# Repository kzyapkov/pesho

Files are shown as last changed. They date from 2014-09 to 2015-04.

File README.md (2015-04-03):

# pesho

Named after St. Peter, the gatekeeper of the physical premises of initlab.org

The rest of this page is in Bulgarian and should not be read by anyone.

## Жици

Схемата включва:
 * **RaspberryPi B+**  на което работи демона за управление, свързано
   през етернет кабел за кораба-майка;
 * **DC Dual Motor Driver 30V 4A** -- драйвер за мотора в бравата,
     [линк](http://www.microbot.it/en/product/73/DC-Dual-Motor-Driver-30V-4A-V2.html)
 * **DC-DC Step-down** за да дадем 5V на малинката и
 * няколко оптрона и други пасивни компоненти.

[Схемата](https://raw.githubusercontent.com/kzyapkov/pesho/master/hardware/pesho.pdf),
начертана с KiCAD.

Накратко, Пешо чете 3 датчика на вратата:
 * "шиповете са извадени", на бравата BLK
 * "шиповете са прибрани", на бравата BUK
 * "вратата е затворена", на бравата BD
Пешо отключва и заключва бравата, като задвижва мотора за 200ms
в желаната посока.

## Код

На Go. Идеята е бравата да може да се манипулира чрез бутоните
и през HTTP. За тестове и дебъгване, HUP сигнал към процеса на
демона също ще отключи или заключи бравата.

## Строене

За успешен билд ти трябва Go Workspace, ето [как](https://golang.org/doc/code.html). После трябва
да упоменеш, че крос-компилираш за arm6:

    # tell go we're cross-compiling for arm6 (rpi):
    export GOOS=linux
    export GOARCH=arm
    export GOARM=6

и накрая, от тази директория:

    pwd
        ...github.com/kzyapkov/pesho
    go build .
    ls -al ./pesho

така получения `pesho` е статично линкнатото bin-че което седи
в /root/pesho и се пуска със `systemctl start pesho`.

## Следва

* Да следим захранването.

## License

      Copyright (c) 2014, initLab <vloo@initlab.org>
      All rights reserved.

      Redistribution and use in source and binary forms, with or without
      modification, are permitted provided that the following conditions are met:

      1. Redistributions of source code must retain the above copyright notice, this
         list of conditions and the following disclaimer.
      2. Redistributions in binary form must reproduce the above copyright notice,
         this list of conditions and the following disclaimer in the documentation
         and/or other materials provided with the distribution.

      THIS SOFTWARE IS PROVIDED BY THE COPYRIGHT HOLDERS AND CONTRIBUTORS "AS IS" AND
      ANY EXPRESS OR IMPLIED WARRANTIES, INCLUDING, BUT NOT LIMITED TO, THE IMPLIED
      WARRANTIES OF MERCHANTABILITY AND FITNESS FOR A PARTICULAR PURPOSE ARE
      DISCLAIMED. IN NO EVENT SHALL THE COPYRIGHT OWNER OR CONTRIBUTORS BE LIABLE FOR
      ANY DIRECT, INDIRECT, INCIDENTAL, SPECIAL, EXEMPLARY, OR CONSEQUENTIAL DAMAGES
      (INCLUDING, BUT NOT LIMITED TO, PROCUREMENT OF SUBSTITUTE GOODS OR SERVICES;
      LOSS OF USE, DATA, OR PROFITS; OR BUSINESS INTERRUPTION) HOWEVER CAUSED AND
      ON ANY THEORY OF LIABILITY, WHETHER IN CONTRACT, STRICT LIABILITY, OR TORT
      (INCLUDING NEGLIGENCE OR OTHERWISE) ARISING IN ANY WAY OUT OF THE USE OF THIS
      SOFTWARE, EVEN IF ADVISED OF THE POSSIBILITY OF SUCH DAMAGE.

      The views and conclusions contained in the software and documentation are those
      of the authors and should not be interpreted as representing official policies,
      either expressed or implied, of the FreeBSD Project.

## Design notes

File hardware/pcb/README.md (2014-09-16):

# Pesho PCB

### Hardware description:

 * Raspberry Pi
 * 3 optoizolated relays
 * 3 optoizolated inputs
 * pesho's pcb

### Design

The design is done using latest version of KiCAD from the repository.
All modules, that weren't available are in pesho.pretty folder.

### License: [Beerware][1]

```
/*
 * ----------------------------------------------------------------------------
 * "THE BEER-WARE LICENSE" (Revision 42):
 * <phk@FreeBSD.ORG> wrote this file. As long as you retain this notice you
 * can do whatever you want with this stuff. If we meet some day, and you think
 * this stuff is worth it, you can buy me a beer in return Poul-Henning Kamp
 * ----------------------------------------------------------------------------
 */
```

[1]: http://en.wikipedia.org/wiki/Beerware

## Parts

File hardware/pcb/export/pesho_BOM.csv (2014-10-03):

Id | Designator | Package | Quantity | Designation | Supplier and ref
1 | C1 | capacitors:CP_10x13mm | 1 | CE 220uF 50V 105C Fujicon
2 | C2,C3,C4,C5,C6,C7,C9,C10,C11,C13,C15,C16 | smd_capacitors:c_1206 | 12 | 10nF
3 | C8 | smd_capacitors:c_1206 | 1 | 10uF
4 | C12 | smd_capacitors:c_1206 | 1 | 100nF
5 | C14 | smd_capacitors:c_1206 | 1 | 100pF
6 | D1 | led:LED-5MM | 1 | LOCK
7 | D2 | led:LED-5MM | 1 | EN
8 | D3 | led:LED-5MM | 1 | UNLOCK
9 | D4 | led:LED-5MM | 1 | BUK
10 | D5 | led:LED-5MM | 1 | BD
11 | D6 | led:LED-5MM | 1 | BLK
12 | D7,D8,D9 | discret:D3 | 3 | SB560 YJ / 60V / 5A / Schottky
13 | D10,D11 | discret:D6.5 | 2 | SB560 YJ / 60V / 5A / Schottky
14 | IC1,IC2,IC3,IC4,IC5,IC6 | dip_sockets:DIP-6__300_ELL | 6 | 4N25
15 | JP1,JP2,JP3 | pin_array:PIN_ARRAY_3X1 | 3 | JUMPER
16 | P1 | pesho:HD-515R-2P | 1 | Power
17 | P2 | pesho:HD-515R-6P | 1 | Bulkey
18 | P3 | connect:HE10_26D | 1 | Raspberry Pi CONN
19 | P4 | connect:SIL-3 | 1 | Serial
20 | R1,R2,R3 | smd_capacitors:c_1206 | 3 | 2.7K
21 | R4,R5,R6 | smd_capacitors:c_1206 | 3 | 820
22 | RV1,RV2,RV3,RV4,RV5,RV6,RV7,RV8,RV9 | pesho:3968W | 9 | 3296W(64W) 20K DIV
23 | U1,U2,U3 | pesho:JE-112D | 3 | JE-112D
24 | D12,D13 | pesho:DO-214AB | 2 | UF5GC SMD

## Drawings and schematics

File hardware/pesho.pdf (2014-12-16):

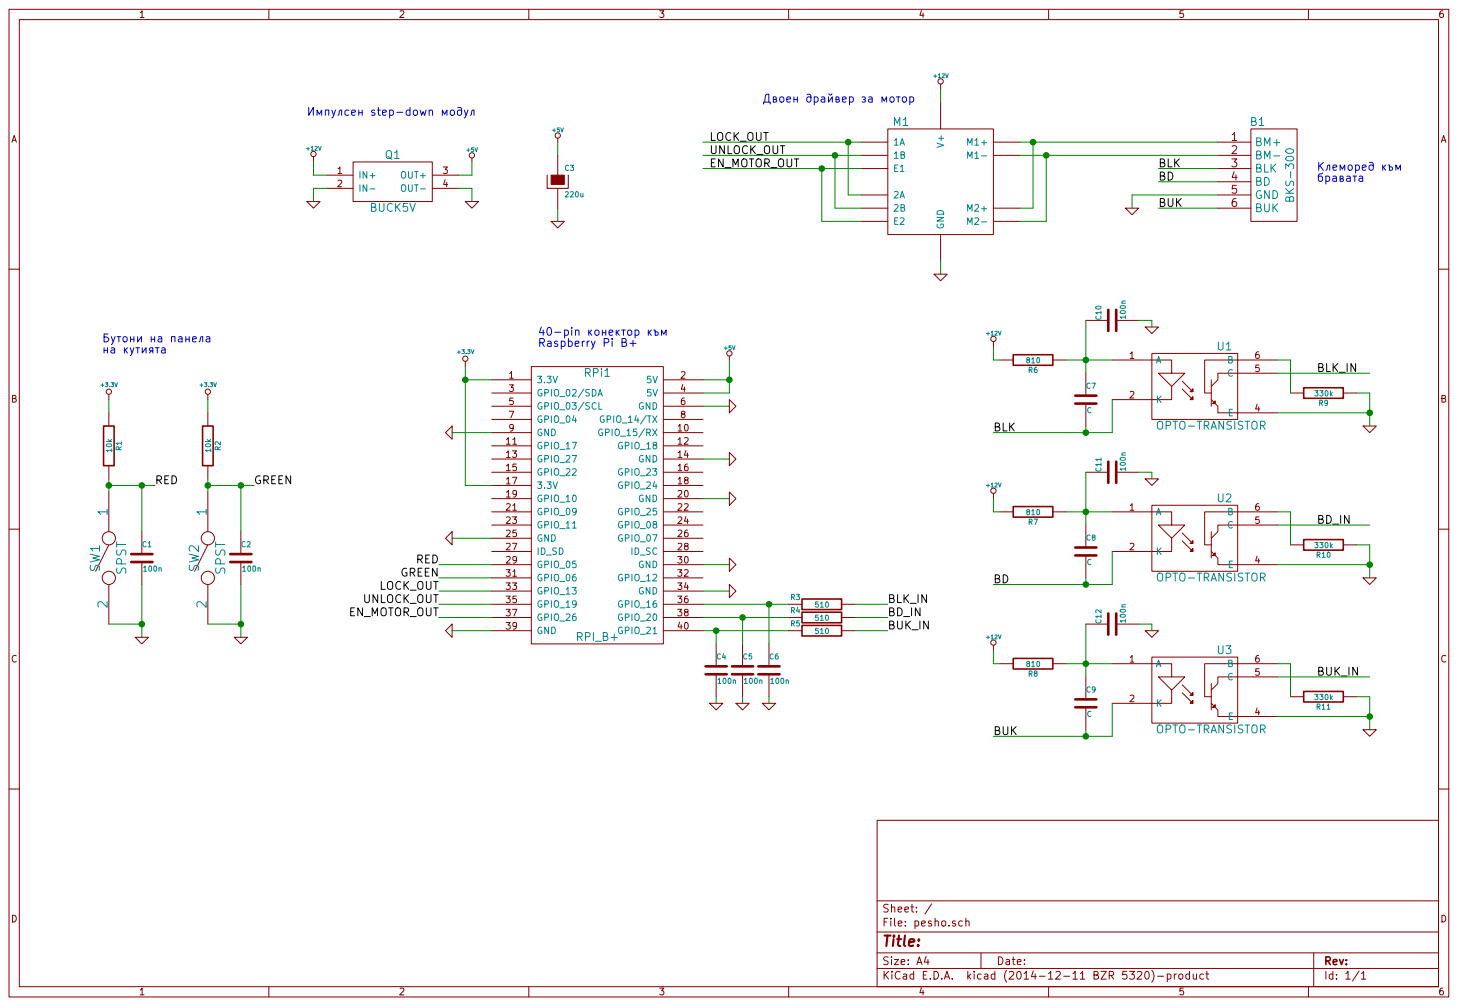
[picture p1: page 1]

File: pesho.sch Sheet: /
Id: 1/1 Title:

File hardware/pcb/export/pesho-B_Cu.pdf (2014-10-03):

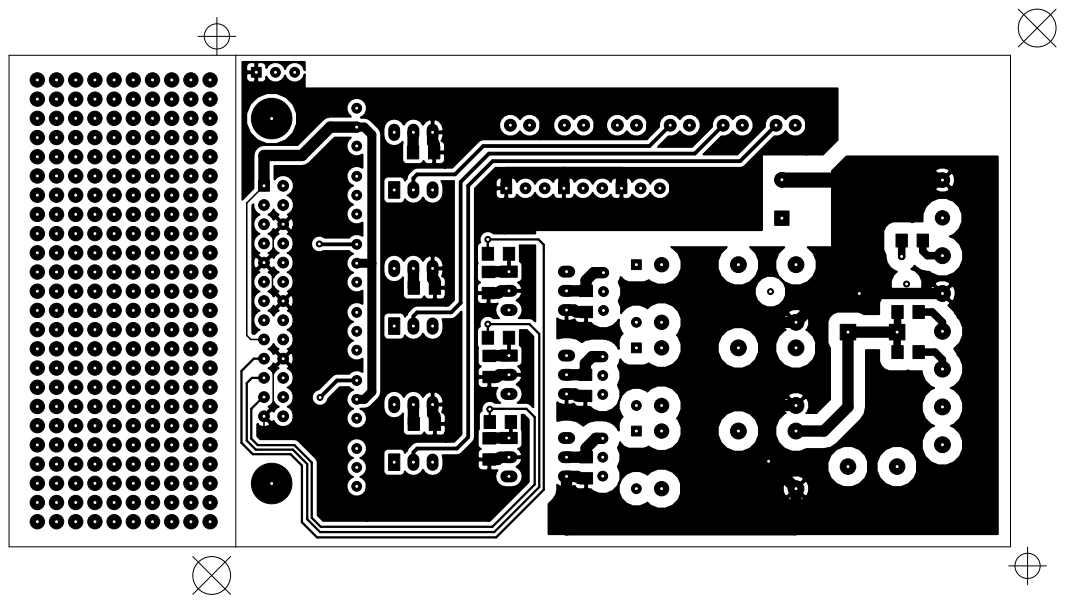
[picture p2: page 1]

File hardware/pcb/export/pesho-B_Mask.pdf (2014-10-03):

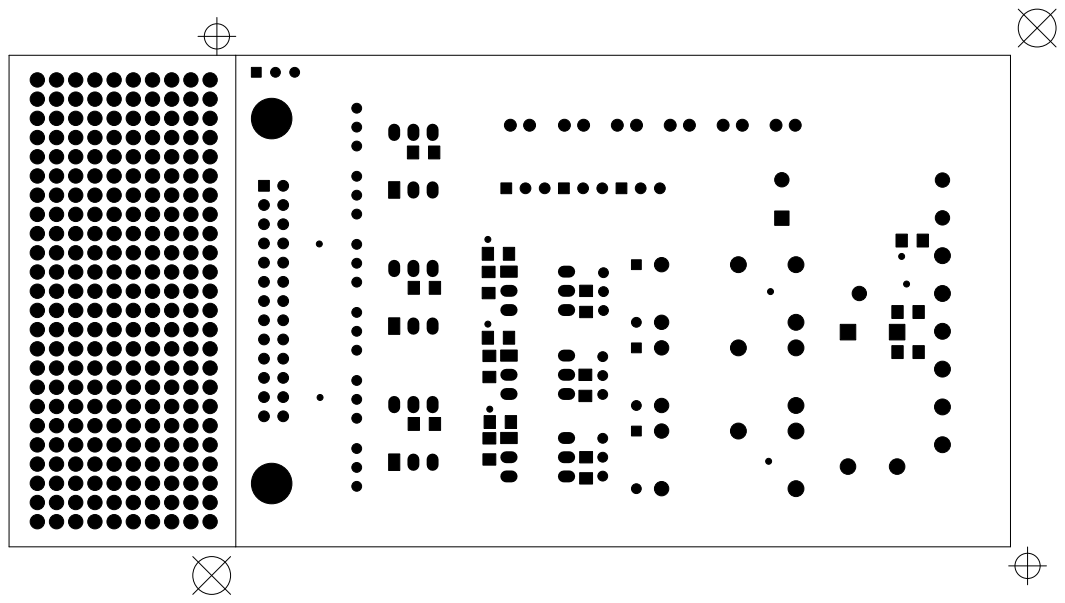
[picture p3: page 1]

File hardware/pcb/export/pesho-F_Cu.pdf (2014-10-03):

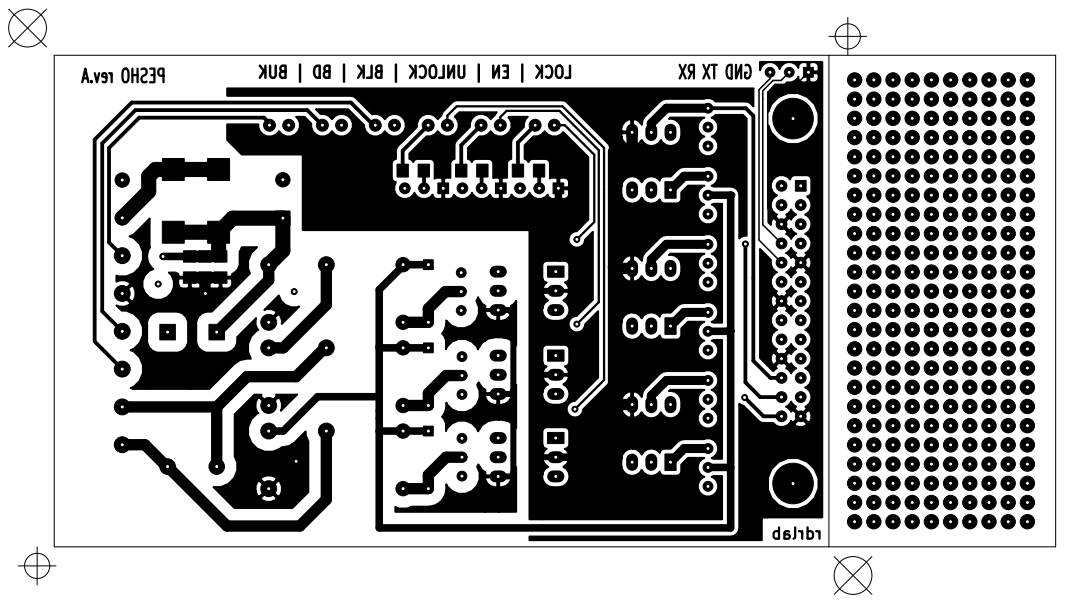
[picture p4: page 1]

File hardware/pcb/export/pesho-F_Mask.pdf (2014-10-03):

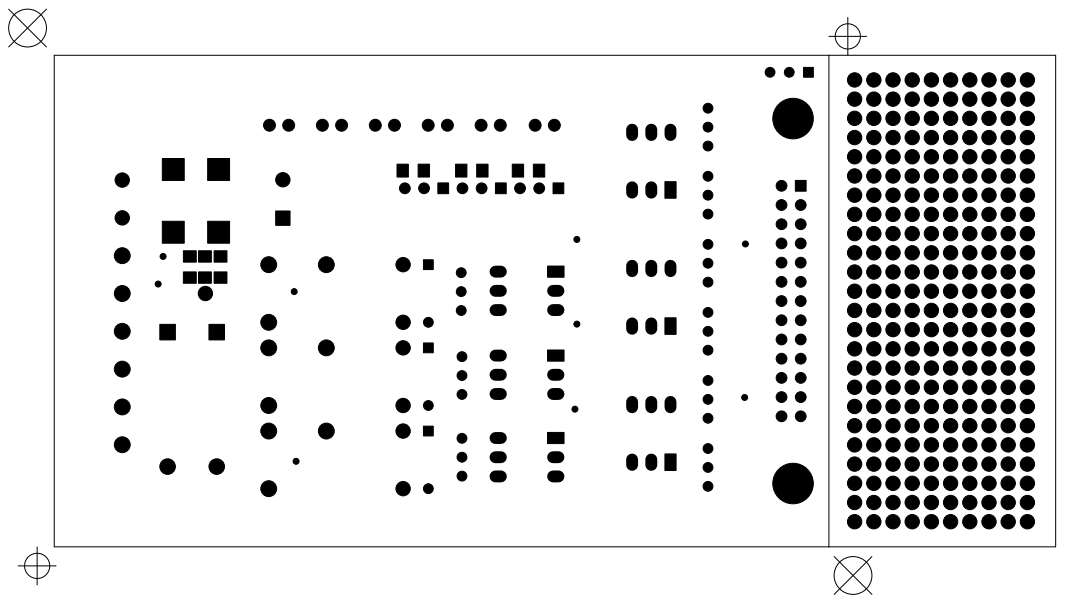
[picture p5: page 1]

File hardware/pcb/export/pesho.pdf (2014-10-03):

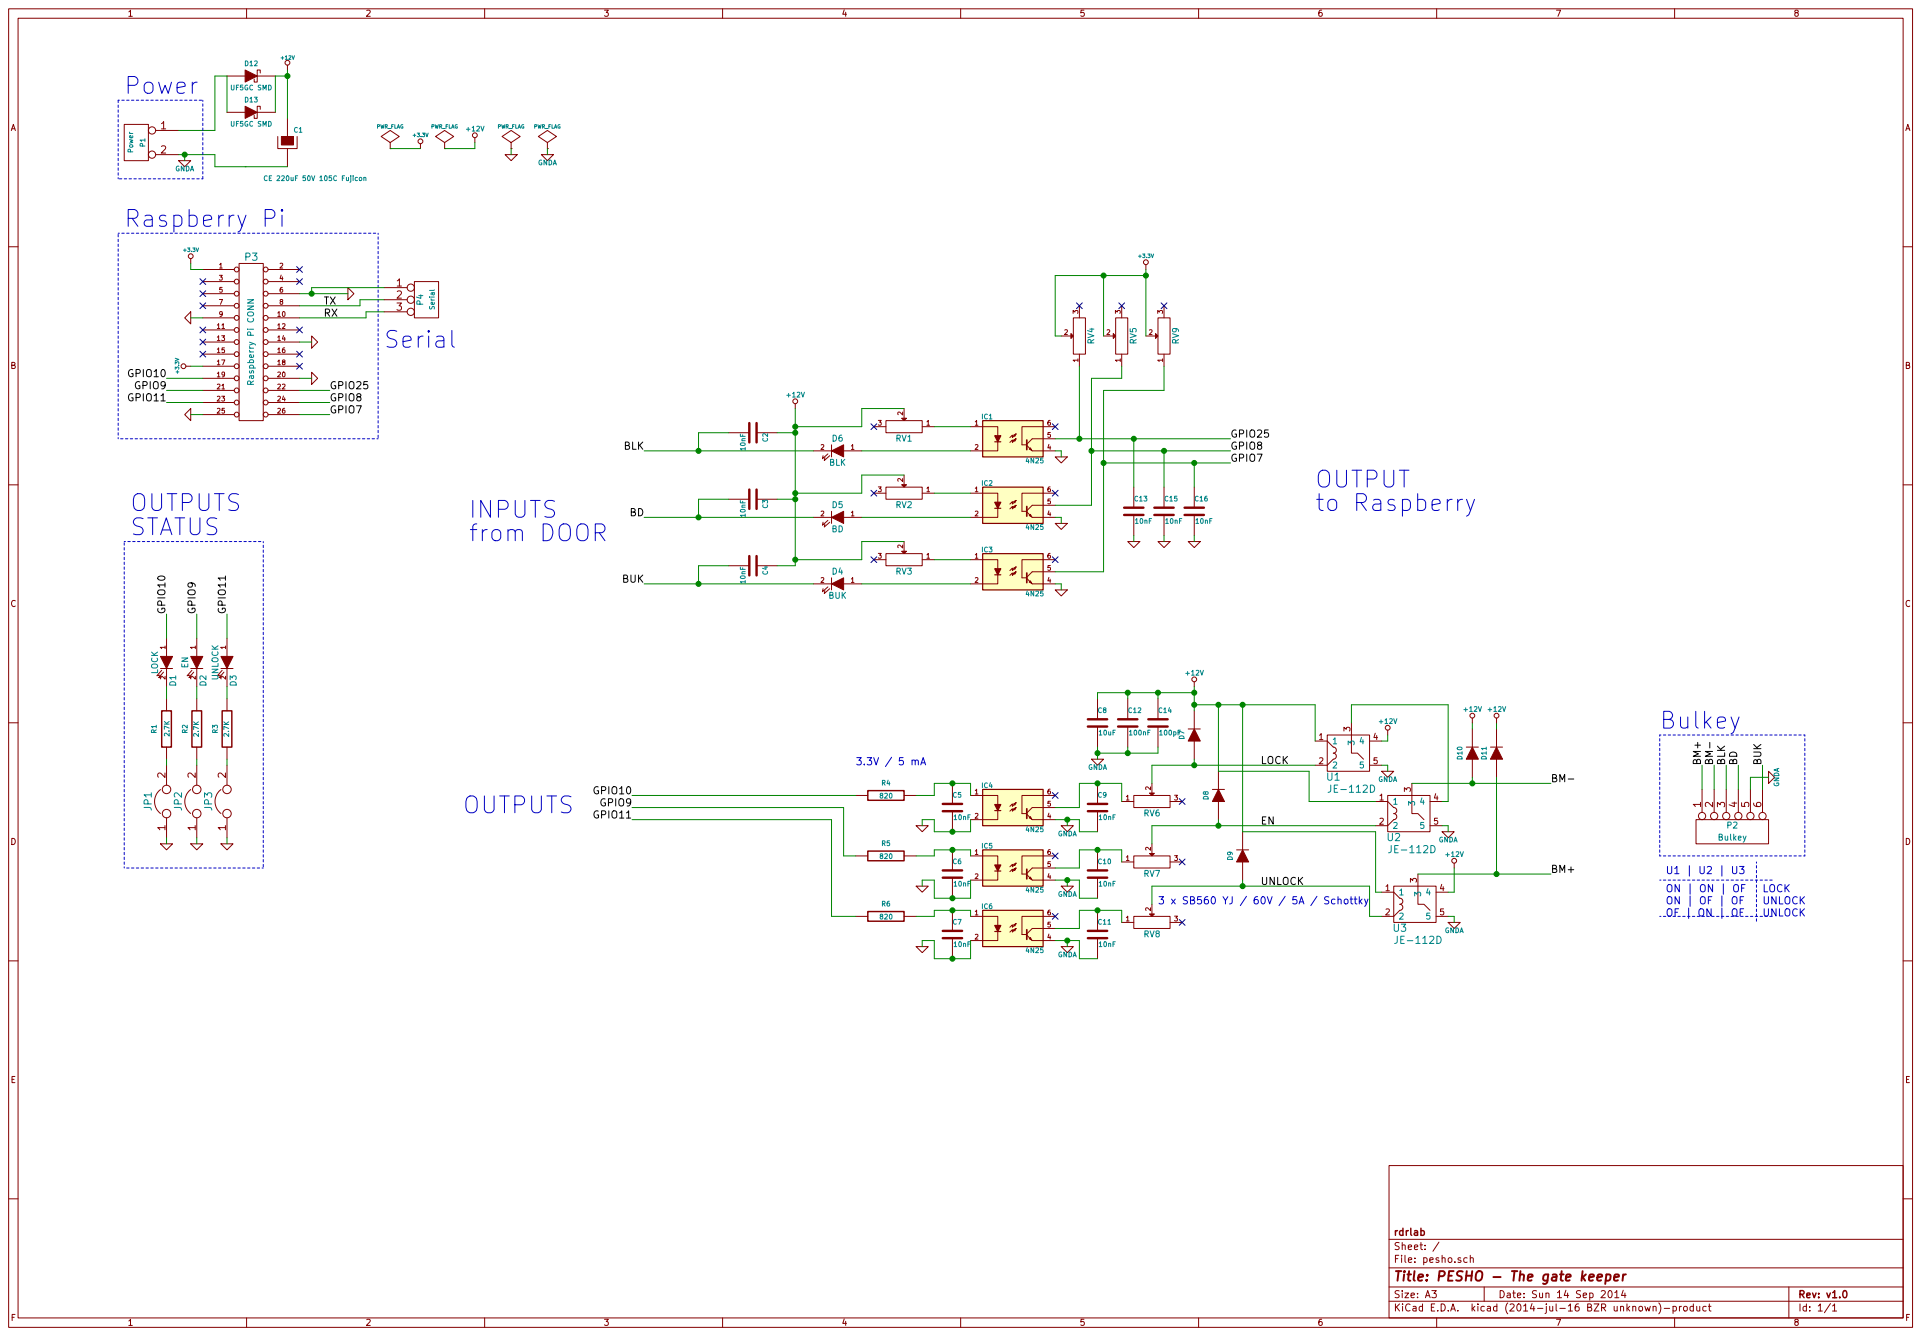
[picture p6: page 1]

File: pesho.sch Sheet: / rdrlab

Id: 1/1 Title: PESHO - The gate keeper

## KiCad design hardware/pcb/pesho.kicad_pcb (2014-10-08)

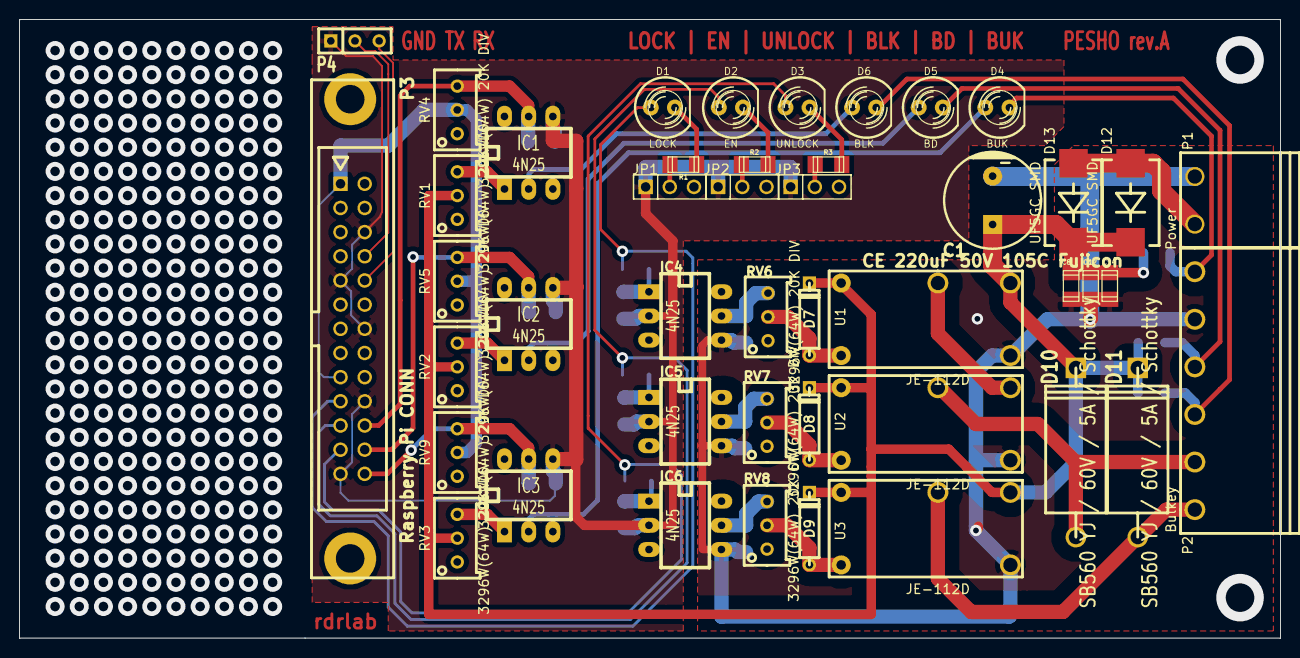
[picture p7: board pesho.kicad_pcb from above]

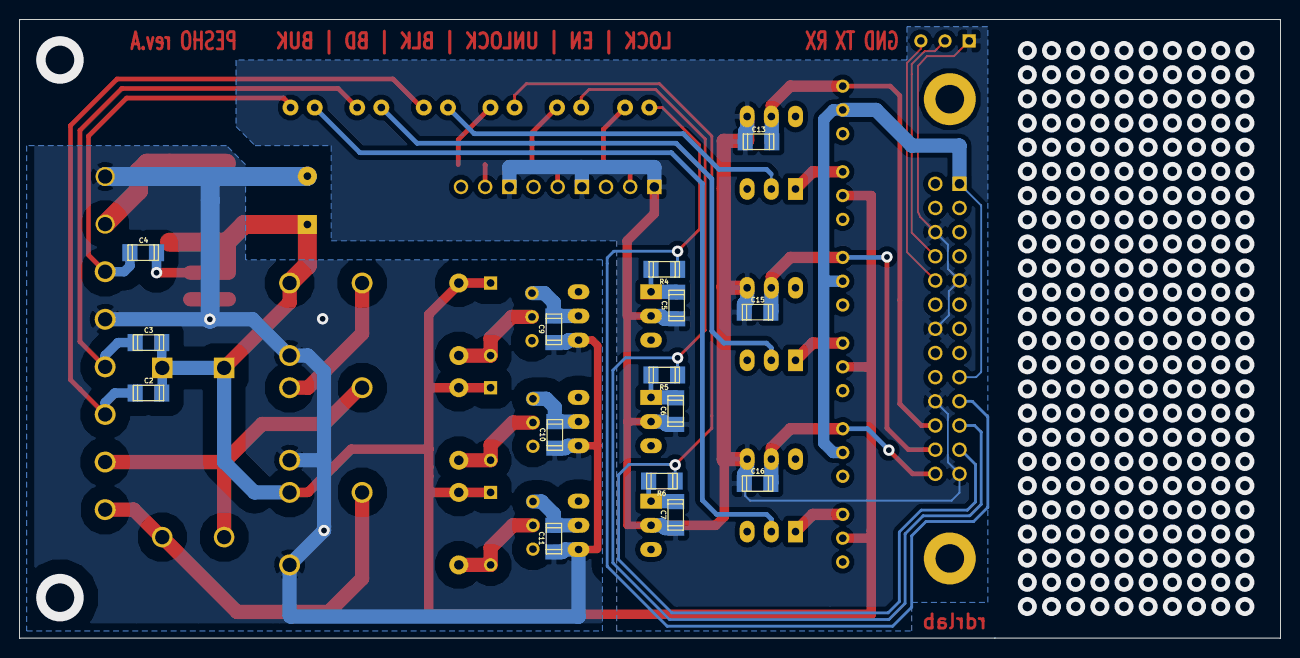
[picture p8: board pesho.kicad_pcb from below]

Board: 2 copper layers, 132.5 x 65.0 mm, 60 parts (15 on the bottom side), 40 nets.

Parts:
C1: CE 220uF 50V 105C Fujicon; CP_10x13mm
C2, C3, C4, C5, C6, C7, C9, C10, C11, C13, C15, C16: 10nF; c_1206
C8: 10uF; c_1206
C12: 100nF; c_1206
C14: 100pF; c_1206
D1: LOCK; LED-5MM
D2: EN; LED-5MM
D3: UNLOCK; LED-5MM
D4: BUK; LED-5MM
D5: BD; LED-5MM
D6: BLK; LED-5MM
D7, D8, D9: SB560 YJ / 60V / 5A / Schottky; D3
D10, D11: SB560 YJ / 60V / 5A / Schottky; D6.5
D12, D13: UF5GC SMD; DO-214AB
IC1, IC2, IC3, IC4, IC5, IC6: 4N25; DIP-6__300_ELL
JP1, JP2, JP3: JUMPER; PIN_ARRAY_3X1
P1: Power; HD-515R-2P
P2: Bulkey; HD-515R-6P
P3: Raspberry Pi CONN; HE10_26D
P4: Serial; SIL-3
R1, R2, R3: 2.7K; c_1206
R4, R5, R6: 820; c_1206
RV1, RV2, RV3, RV4, RV5, RV6, RV7, RV8, RV9: 3296W(64W) 20K DIV; 3968W
U1, U2, U3: JE-112D

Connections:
+3.3V: P3.1, P3.17, RV4.2, RV5.2, RV9.2
+12V: C1.1, C2.1, C3.1, C4.1, C8.1, C12.1, C14.1, D7.2, D8.2, D9.2, D10.2, D11.2, D12.2, D13.2, RV1.2, RV2.2, RV3.2, U1.1, U1.4, U2.1, U3.1, U3.4
/BD: C3.2, D5.2, P2.4
/BLK: C2.2, D6.2, P2.3
/BM+: D11.1, P2.1, U3.3
/BM-: D10.1, P2.2, U2.3
/BUK: C4.2, D4.2, P2.6
/EN: D8.1, RV7.2, U2.2
/GPIO7: C16.1, IC3.5, P3.26, RV9.1
/GPIO8: C15.1, IC2.5, P3.24, RV5.1
/GPIO9: D2.1, P3.21, R5.2
/GPIO10: D1.1, P3.19, R4.2
/GPIO11: D3.1, P3.23, R6.2
/GPIO25: C13.1, IC1.5, P3.22, RV4.1
/LOCK: D7.1, RV6.2, U1.2
/RX: P3.10, P4.3
/TX: P3.8, P4.2
/UNLOCK: D9.1, RV8.2, U3.2
GND: C5.2, C6.2, C7.2, C13.2, C15.2, C16.2, IC1.4, IC2.4, IC3.4, IC4.2, IC5.2, IC6.2, JP1.1, JP2.1, JP3.1, P3.6, P3.9, P3.14, P3.20, P3.25, P4.1
GNDA: C1.2, C8.2, C9.2, C10.2, C11.2, C12.2, C14.2, IC4.4, IC5.4, IC6.4, P1.2, P2.5, U1.5, U2.5, U3.5
unnamed: C5.1, IC4.1, R4.1
unnamed: C6.1, IC5.1, R5.1
unnamed: C7.1, IC6.1, R6.1
unnamed: C9.1, IC4.5, RV6.1
unnamed: C10.1, IC5.5, RV7.1
unnamed: C11.1, IC6.5, RV8.1
unnamed: D1.2, R1.1
unnamed: D2.2, R2.2
unnamed: D3.2, R3.2
unnamed: D4.1, IC3.2
unnamed: D5.1, IC2.2
unnamed: D6.1, IC1.2
unnamed: D12.1, D13.1, P1.1
unnamed: IC1.1, RV1.1
unnamed: IC2.1, RV2.1
unnamed: IC3.1, RV3.1
unnamed: JP1.2, R1.2
unnamed: JP2.2, R2.1
unnamed: JP3.2, R3.1
unnamed: U1.3, U2.4

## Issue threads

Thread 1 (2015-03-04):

Относно нотифицирането на нещо за отворена/затворена врата

ignisf, 2015-03-04:
Предлагам следната схема:

`POST door/status` с параметър `name` със стойност `open`/`closed`/`locked`/`unlocked`. Така нещото ще може да води журнал с промените на състоянието на вратата. Как ти се струва?

Closed 2015-04-03.

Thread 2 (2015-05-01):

Token, който да се подава при изпращане на нотификации

ignisf, 2015-05-01:
Засега липсва автентикация на изпратените събития, дали би било възможно да се добави един token, който да се праща като параметър или http хедър?

kzyapkov, 2015-05-01:
Ако е с ненулева дължина, `SecretNotificationToken` от `pesho.conf` ще се добави към POST данните. Чудя се защо пиша това на български...

Closed 2015-05-01.

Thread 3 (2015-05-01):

Не се изпраща нотификация при отключване

ignisf, 2015-05-01:

kzyapkov, 2015-05-01:
Пешо праща нотификации за промени и в двата параметъра за които знае, като спестява само транзиентните състояния `Locking` и `Unlocking`:

```
[root@doorpi ~]# journalctl -u pesho -n 500 | grep Notifying
May 01 16:31:38 doorpi pesho[31605]: 2015/05/01 16:31:38.048851 Notifying for {Locked Closed}: map[door:[Closed] latch:[Locked]]
May 01 16:34:44 doorpi pesho[31656]: 2015/05/01 16:34:44.122428 Notifying for {Locked Closed}: map[door:[Closed] latch:[Locked]]
May 01 16:43:57 doorpi pesho[31656]: 2015/05/01 16:43:57.188597 Notifying for {Locked Closed}: map[door:[Closed] latch:[Locked]]
May 01 18:03:03 doorpi pesho[31656]: 2015/05/01 18:03:03.934741 Notifying for {Unlocked Open}: map[door:[Open] latch:[Unlocked]]
May 01 18:03:20 doorpi pesho[31656]: 2015/05/01 18:03:20.485660 Notifying for {Unlocked Closed}: map[latch:[Unlocked] door:[Closed]]
May 01 18:03:25 doorpi pesho[31656]: 2015/05/01 18:03:25.076140 Notifying for {Unlocked Open}: map[door:[Open] latch:[Unlocked]]
May 01 18:03:28 doorpi pesho[31656]: 2015/05/01 18:03:28.388597 Notifying for {Unlocked Closed}: map[latch:[Unlocked] door:[Closed]]
May 01 18:07:25 doorpi pesho[31656]: 2015/05/01 18:07:25.193491 Notifying for {Unlocked Open}: map[door:[Open] latch:[Unlocked]]
May 01 18:07:29 doorpi pesho[31656]: 2015/05/01 18:07:29.516984 Notifying for {Unlocked Closed}: map[door:[Closed] latch:[Unlocked]]
```

Може ли малко разяснение какъв точно е проблема?

ignisf, 2015-05-01:
има ли нотификация при преминаване от {Locked Closed} към {Unlocked Closed}?

kzyapkov, 2015-05-01:
Brainfart, извинявай.

ignisf, 2015-05-01:
няма грижи

Closed 2015-05-20.

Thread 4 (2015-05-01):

Пешо не умира правилно

kzyapkov, 2015-05-01:
```
May 01 14:43:12 doorpi pesho[31564]: 2015/05/01 14:43:12.963465 Received SIGINT/SIGTERM; Exiting gracefully...
May 01 14:43:12 doorpi pesho[31564]: panic: close of nil channel
May 01 14:43:12 doorpi pesho[31564]: goroutine 9 [running]:
May 01 14:43:13 doorpi pesho[31564]: main.(*pesho).close(0x10537920)
May 01 14:43:13 doorpi pesho[31564]: /home/kiril/src/go/src/github.com/kzyapkov/pesho/pesho.go:52 +0x54
May 01 14:43:13 doorpi pesho[31564]: main.*pesho.(main.close)<C2><B7>fm()
May 01 14:43:13 doorpi pesho[31564]: /home/kiril/src/go/src/github.com/kzyapkov/pesho/pesho.go:46 +0x24
May 01 14:43:13 doorpi pesho[31564]: sync.(*Once).Do(0x1050a900, 0x10518f70)
May 01 14:43:13 doorpi pesho[31564]: /usr/lib/go/src/sync/once.go:44 +0x140
May 01 14:43:13 doorpi pesho[31564]: main.(*pesho).Close(0x10537920)
May 01 14:43:13 doorpi pesho[31564]: /home/kiril/src/go/src/github.com/kzyapkov/pesho/pesho.go:46 +0x6c
May 01 14:43:13 doorpi pesho[31564]: main.(*pesho).interruptHandler(0x10537920)
May 01 14:43:13 doorpi pesho[31564]: /home/kiril/src/go/src/github.com/kzyapkov/pesho/pesho.go:40 +0x1e8
May 01 14:43:13 doorpi pesho[31564]: created by main.main
May 01 14:43:13 doorpi pesho[31564]: /home/kiril/src/go/src/github.com/kzyapkov/pesho/pesho.go:234 +0x5cc
May 01 14:43:13 doorpi pesho[31564]: goroutine 1 [semacquire, 4 minutes]:
May 01 14:43:13 doorpi pesho[31564]: sync.(*WaitGroup).Wait(0x1053792c)
May 01 14:43:13 doorpi pesho[31564]: /usr/lib/go/src/sync/waitgroup.go:132 +0x194
May 01 14:43:13 doorpi pesho[31564]: main.main()
May 01 14:43:13 doorpi pesho[31564]: /home/kiril/src/go/src/github.com/kzyapkov/pesho/pesho.go:254 +0x8d0
May 01 14:43:13 doorpi pesho[31564]: goroutine 5 [syscall, 2 minutes]:
May 01 14:43:13 doorpi pesho[31564]: syscall.Syscall6(0xfc, 0x3, 0x105176ac, 0x10, 0xffffffff, 0x0, 0x0, 0x5dd1dde, 0x382c40, 0x6e0cc)
May 01 14:43:13 doorpi pesho[31564]: /usr/lib/go/src/syscall/asm_linux_arm.s:48 +0x8
May 01 14:43:13 doorpi pesho[31564]: syscall.EpollWait(0x3, 0x105176ac, 0x10, 0x10, 0xffffffff, 0x1, 0x0, 0x0)
May 01 14:43:13 doorpi pesho[31564]: /usr/lib/go/src/syscall/zsyscall_linux_arm.go:376 +0x98
May 01 14:43:13 doorpi pesho[31564]: github.com/kzyapkov/gpio.func<C2><B7>001()
May 01 14:43:13 doorpi pesho[31564]: /home/kiril/src/go/src/github.com/kzyapkov/gpio/gpio_linux.go:70 +0x74
May 01 14:43:13 doorpi pesho[31564]: created by github.com/kzyapkov/gpio.setupEpoll
May 01 14:43:13 doorpi pesho[31564]: /home/kiril/src/go/src/github.com/kzyapkov/gpio/gpio_linux.go:90 +0x1ac
May 01 14:43:13 doorpi pesho[31564]: goroutine 6 [syscall]:
May 01 14:43:13 doorpi pesho[31564]: os/signal.loop()
May 01 14:43:13 doorpi pesho[31564]: /usr/lib/go/src/os/signal/signal_unix.go:21 +0x1c
May 01 14:43:13 doorpi pesho[31564]: created by os/signal.init<C2><B7>1
 ESCOD
May 01 14:38:37 doorpi pesho[31552]: /usr/lib/go/src/bufio/bufio.go:324 +0x70
May 01 14:38:37 doorpi pesho[31552]: net/textproto.(*Reader).readLineSlice(0x10536560, 0x0, 0x0, 0x0, 0x0, 0x0)
May 01 14:38:37 doorpi pesho[31552]: /usr/lib/go/src/net/textproto/reader.go:55 +0x60
May 01 14:38:37 doorpi pesho[31552]: net/textproto.(*Reader).ReadLine(0x10536560, 0x0, 0x0, 0x0, 0x0)
May 01 14:38:37 doorpi pesho[31552]: /usr/lib/go/src/net/textproto/reader.go:36 +0x3c
May 01 14:38:37 doorpi pesho[31552]: net/http.ReadRequest(0x10530090, 0x10538700, 0x0, 0x0)
May 01 14:38:37 doorpi pesho[31552]: /usr/lib/go/src/net/http/request.go:598 +0x88
May 01 14:38:37 doorpi pesho[31552]: net/http.(*conn).readRequest(0x10540000, 0x0, 0x0, 0x0)
May 01 14:38:37 doorpi pesho[31552]: /usr/lib/go/src/net/http/server.go:586 +0x278
May 01 14:38:37 doorpi pesho[31552]: net/http.(*conn).serve(0x10540000)
May 01 14:38:37 doorpi pesho[31552]: /usr/lib/go/src/net/http/server.go:1162 +0x5ec
May 01 14:38:37 doorpi pesho[31552]: created by net/http.(*Server).Serve
May 01 14:38:37 doorpi pesho[31552]: /usr/lib/go/src/net/http/server.go:1751 +0x348
May 01 14:38:37 doorpi pesho[31552]: goroutine 24 [select, 6 minutes]:
May 01 14:38:38 doorpi pesho[31552]: net.func<C2><B7>019()
May 01 14:38:38 doorpi pesho[31552]: /usr/lib/go/src/net/dnsclient_unix.go:241 +0x310
May 01 14:38:38 doorpi pesho[31552]: created by net.loadConfig
May 01 14:38:38 doorpi pesho[31552]: /usr/lib/go/src/net/dnsclient_unix.go:269 +0x228
```

Closed 2015-05-01.

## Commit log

2014-09-06 State pretty print
2014-09-12 refactored, simpler logic, web and buttons
2014-09-16 Initial commit of the PCB.
    [pesho.kicad_pcb, pesho.sch]
2014-09-16 ignore PCB backup files
2014-09-16 added test pcb segment
    [pesho.kicad_pcb]
2014-09-17 better layout and all components on place
    [pesho.kicad_pcb, pesho.sch]
2014-09-30 added some traces
    [pesho.kicad_pcb]
2014-09-30 Diode 60V / 5A module added to the library.
2014-09-30 2 serial diodes added for protection.
    [pesho.kicad_pcb, pesho.sch]
2014-10-01 Final version of the pcb.
    [pesho.kicad_pcb]
2014-10-03 Latest layout submitted to bulged for films.
    [pesho.kicad_pcb]
2014-10-03 Schematic and layout .pdf files submitted to bulged.
2014-10-03 BOM added to the repository.
    [pesho_BOM.csv]
2014-10-06 Last version with fixed drills and send for production.
    [pesho.kicad_pcb]
2014-10-06 Gerber files send to CPR for production.
    [pesho-B_Cu.gbr, pesho-B_Mask.gbr, pesho-Edge_Cuts.gbr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]
2014-10-08 Fixed small bug in the pcb on one of the Relays.
    [pesho.kicad_pcb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]
2014-10-29 Latest updates to the PCB included
    [pesho.sch]
2014-11-12 Schematic retought and resistor values changed.
    [pesho.sch]
2014-12-10 Last update ! The PCB is not working, because of the relays.
    [pesho.sch]
2014-12-14 yet another hw version
    [pesho.sch]
2014-12-14 more hw files
    [pesho.sch]
2014-12-15 changed values of the resistors and added connections to the rpi
    [pesho.sch]
2014-12-15 ignore kicad cache and backup files
2014-12-15 simple open loop logic, new pin layout
2014-12-16 some explanations
    [pesho.sch]
2014-12-16 moved stuff around
    [pesho-B_Cu.gbr, pesho-B_Mask.gbr, pesho-Edge_Cuts.gbr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]
2015-01-25 button pin numbers
2015-03-03 fix buttons and inputs
